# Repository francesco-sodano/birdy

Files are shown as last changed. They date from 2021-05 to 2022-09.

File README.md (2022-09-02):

<p align="center">
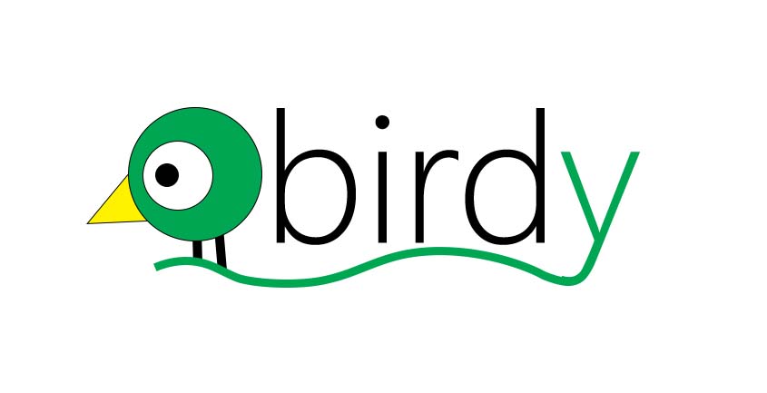
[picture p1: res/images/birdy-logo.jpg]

</p>

# Birdy - The Open-Source Smart Feeder to fight climate change
Birdy is a nicely designed wild bird feeder that takes photos, identifies and classifies birds. - based on Raspberry Pi, Azure IoT Edge and Azure Cognitive Service.

# Inspiration

Let's play a game! :)

***Question 1: Did you know that in many countries birdwatching is more popular than gardening?***

However, as you can't just sit around your bird feeder all the time, you miss out on a lot of action.

***Question 2: Did you know that birds play several essential and indispensable roles in the ecosystems they reside in and travel through?***

Birds raising broods end up acting as pest control agents by devouring insects and other organisms that harm the environment and crops. Migratory birds help in dispersal of seeds, leading to maintenance of biodiversity along their routes.

***Question 3: Did you know that bird feeders are helping migrating birds?***

Climate change does a lot more than just heat up our planet. Climate change can also cause more intense weather. That could mean more hurricanes, floods, heat waves, droughts, and even cold spells.
This extreme weather can be trouble for birds. Scientists have noticed that when extreme weather happens, fewer birds show up in the places they call home.
If birds are moving to other areas because of climate change, they may need our help and we may need to protect their new habitats.
Having bird feeders along their route will help to keep migrating birds energized to complete their journey forward. In months like the winter, bird feeders act almost like an oasis of food for these feathery creatures.

So what if will be able to combine all these in one single, open solution that:

1. Helps to identify, classify and register birds that are coming to visit our houses 
2. Shares those data worldwide, to identify new or established migration routes and define new natural reserves to fight the climate change
3. Works on our side to NOT miss out any visit you are having in your garden

these are the reasons why we created **Project Birdy**

<p align="center">
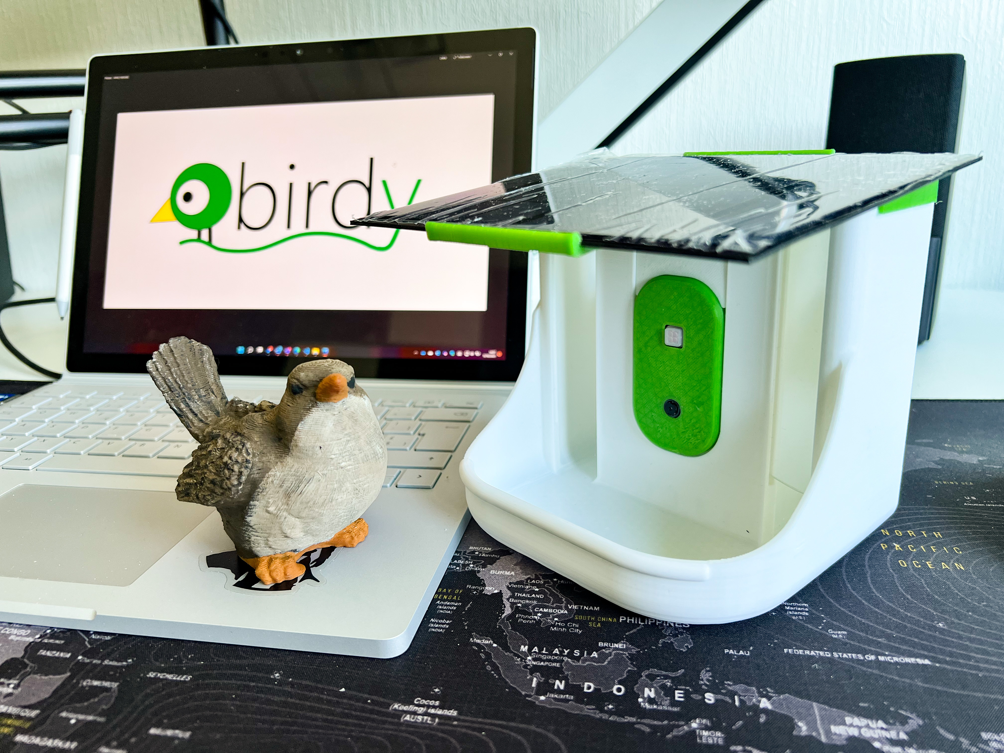
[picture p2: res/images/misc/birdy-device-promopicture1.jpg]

</p>

# The Project Repository

the repository is organized in this way:

1. *backend*: contains the contains the IaC for the backend deployment and the source code for the backend running on the infrastructure created.
2. *device*: contains the device STL for 3d printing and the software to run on the device.
3. *docs*: contains the step-by-step documentation for put in place the entire solution
4. *mobile*: contains the source code for the mobile app
5. *res*: contains static resources like images to be used in the doc files
6. *tools*: contains any additional resource you may need to put in place the solution

# The Device

The device is based on Raspberry Pi and use Azure IoT Edge framework.

<p align="center">
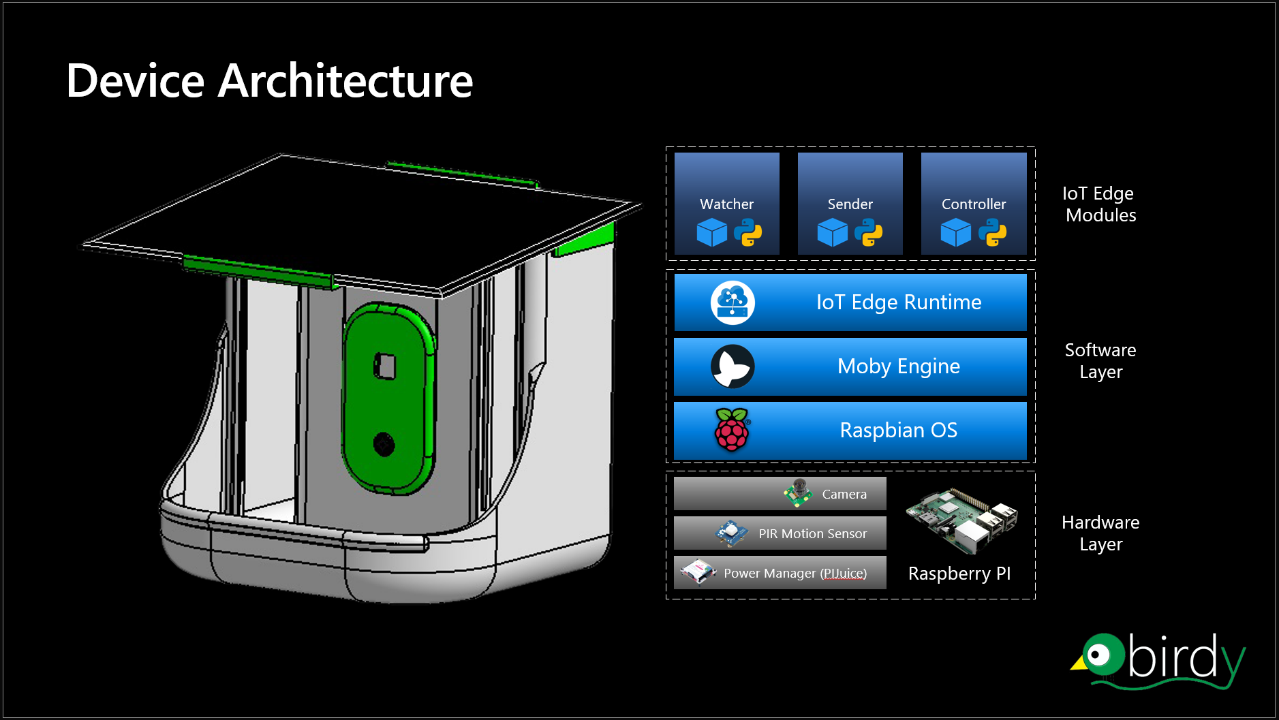
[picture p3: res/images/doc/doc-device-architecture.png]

</p>

More info can be found here: [The Device](https://github.com/francesco-sodano/birdy/blob/main/docs/device.md)

# The Back-end

# The Mobile App

# Notice

1. **Privacy** is always important for us. Birdy is designed and configured to have a very short focus range (5 cm max). it means that everything out of this range will be out-of-focus and blurred.
2. **Squirrels** are usually a common issues for bird feeders: There is actually no way to stop squirrels to come to the feeder but hey.. let's them eat too.. we are nature friends! :). Birdy as anyway a specific function to detect squirrel presence and don't collect pictures (also with an alert for the Birdy owner if configured).

# Table of Content

1. [Read Me](https://github.com/francesco-sodano/birdy/blob/main/README.md)
2. [The Device](https://github.com/francesco-sodano/birdy/blob/main/docs/device.md)
3. [Architecture](https://github.com/francesco-sodano/birdy/blob/main/docs/architecture.md)
4. [Deployment](https://github.com/francesco-sodano/birdy/blob/main/docs/deployment.md)
5. [Setup](https://github.com/francesco-sodano/birdy/blob/main/docs/instructions.md)

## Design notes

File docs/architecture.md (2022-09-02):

# Architecture

# Edge logical Architecture

The SmartBox is based on a Raspberry Pi architecture running Raspberry Pi OS Bullseye (Debian 11).

<p align="center">

</p>

On top of the OS, we have the IoT Edge Runtime (version 1.4): The IoT Edge service provides and maintains security standards on the IoT Edge device. The service starts on every boot and bootstraps the device by starting the rest of the IoT Edge runtime.

Azure IoT Edge relies on an OCI-compatible container runtime. Birdy is using Moby Engine for maximize support and compatibility: The Moby engine is the only container engine officially supported with IoT Edge.

The Birdy software are running as custom modules on the Azure Iot Edge service. there are three different custom modules running on the device:

- Watcher
- Sender
- Controller

## Watcher

## Sender

## Controller

# Back-End logical Architecture

## The Trained AI

## Data Layer

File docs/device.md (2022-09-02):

# The Device

The device is composed by hardware and software components.

There are different versions and variants of the device in this repository.

the macro-components of the device are the following:

1. Bird Feeder
2. Smart Box
3. Roof Top

## Bird Feeder

The Bird feeder is the main 3D Printed component of the device. it has the function of storing and deploy seeds and to handle the any version of the Smart Box.

<p align="center">
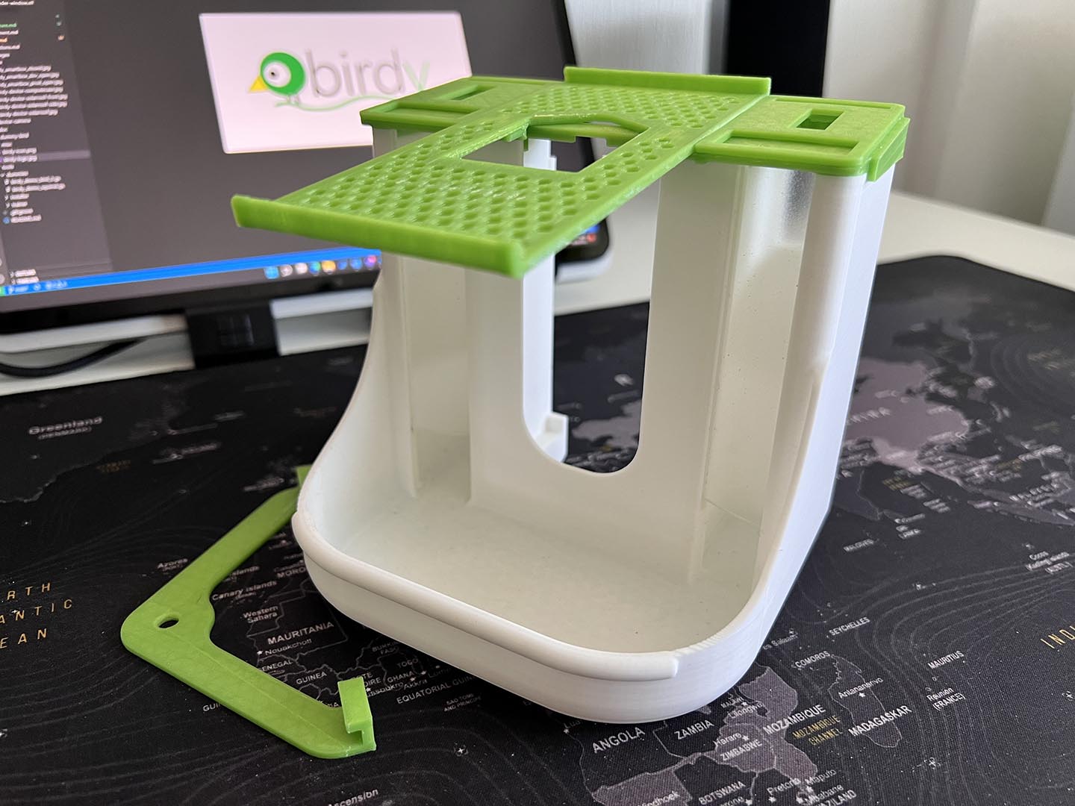
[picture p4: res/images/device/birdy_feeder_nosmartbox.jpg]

</p>

the Smart Box is detachable without compromise basic function of the feeder: it means you can use Birdy as standard feeder without the Smart Box.

## Smart Box

The Smart Box contians all the sensors, the battery and the compute for birdy.
It's easely detachable so you can bring it with you, leaving the feeder in its position.

<p align="center">
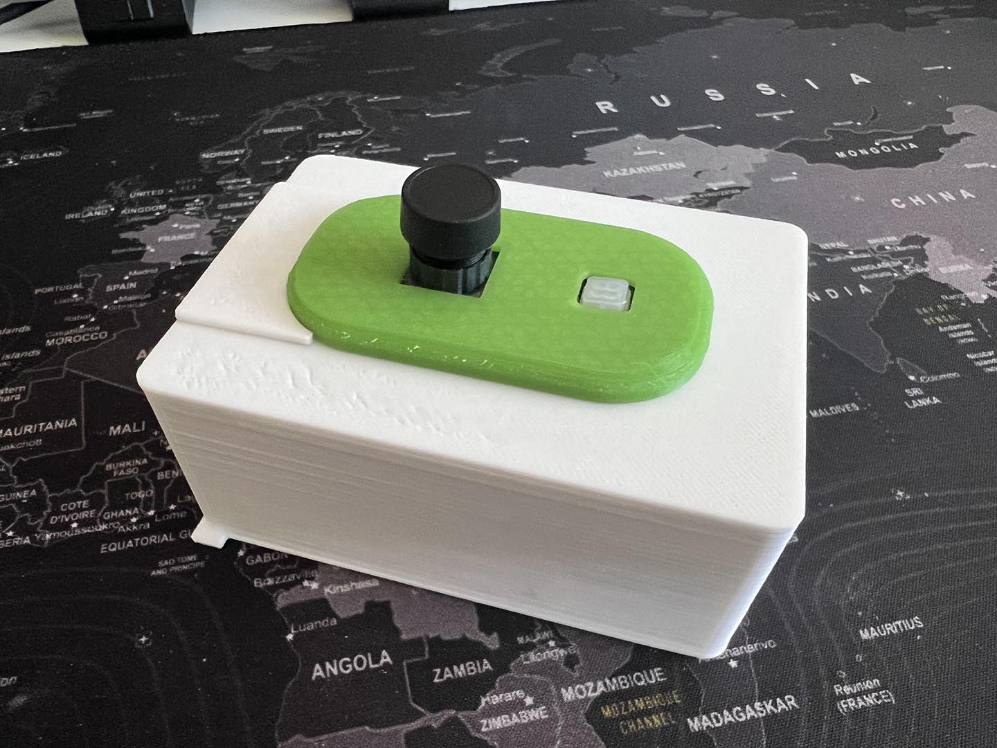
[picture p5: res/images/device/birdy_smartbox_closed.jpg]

</p>

The SmartBox is designed to work with a PiJuice Hat that works as power controller and can be configured and managed remotely: for example you can configure the smartbox to shutdown in the night and turn on again at dawn or shutdown when the battery power is at certain battery level and turn it on again when the solar panel rechanged the battery.

The Smart Box has two different versions:

1. **DEV Version**: this is based on Raspberry Pi 3 B+ and it's used for development. Raspberry Pi 3 B+ is able to handle direct connetion with Visual Studio Code for debugging. the battery life it's ok for few hours sessions.

<p align="center">
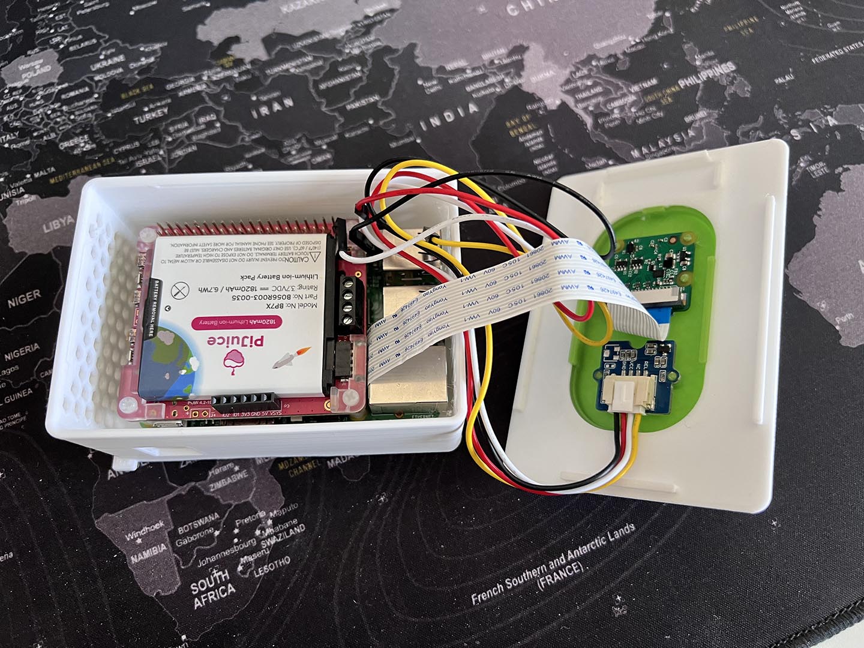
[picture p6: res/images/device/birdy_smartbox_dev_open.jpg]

</p>

2. **PROD Version**: this is based on Raspberry Pi Zero W and it's used for production. it's requires less power and has a better battery life to permit long sessions (up to one week).

<p align="center">
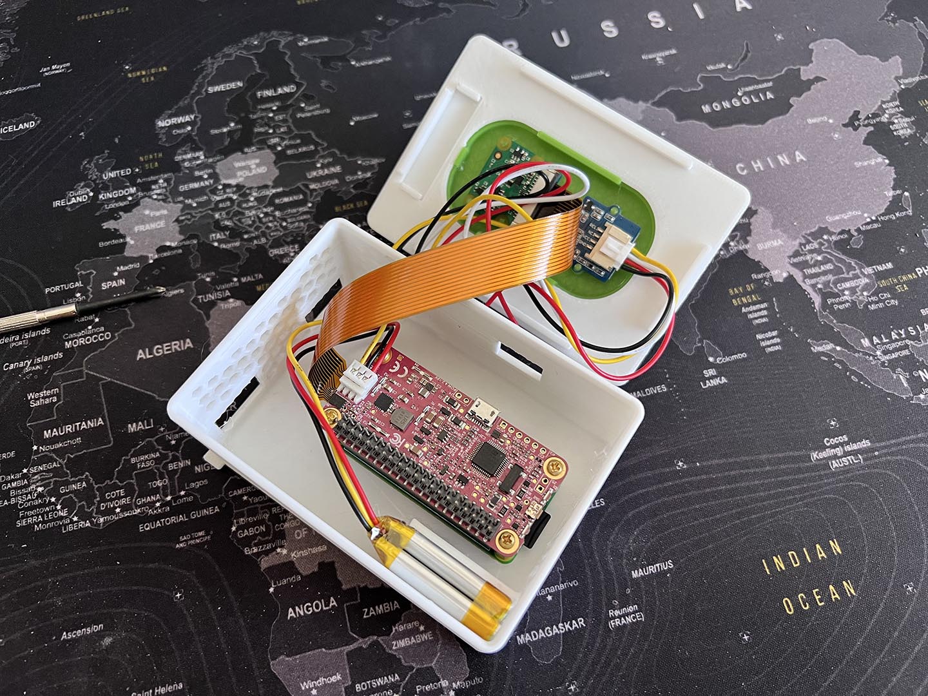
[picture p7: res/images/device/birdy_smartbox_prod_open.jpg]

</p>

The Smart box could be also directly connected to a power supply so Birdy can be always up and running.

## Roof Top

The Roof Top has also two different variants:

1. **Standard**: this is standard 3D printed roof.

2. **Solar Powered**: this is an enhanched version that includes a solar panel able to rechanrge the battery of the Smart Box and increase the autonomy of the device.

# Hardware Components

the **DEV Version** of the device requires the following hardware:

1. [Raspberry Pi 3 model B+](https://uk.pi-supply.com/products/raspberry-pi-3-model-b-plus?_pos=64&_sid=6161a3a4c&_ss=r1)
2. [Grove mini PIR motion sensor](https://www.seeedstudio.com/Grove-mini-PIR-motion-sensor-p-2930.html)
3. [Raspberry Pi camera board v2.1](https://uk.pi-supply.com/products/raspberry-pi-camera-board-v2-1-8mp-1080p?_pos=48&_sid=6161a3a4c&_ss=r)
4. [Raspberry Pi camera lens 160 degree](https://uk.pi-supply.com/products/camera-module-for-official-raspberry-pi-camera-board-v2-8mp-sensor-160-degree)
5. [PiJuice Standard with 1820mAh battery](https://uk.pi-supply.com/products/pijuice-standard)

the **PROD Version** of the device requires the following hardware:

1. [Raspberry Pi Zero W (with soldered header)](https://uk.pi-supply.com/products/raspberry-pi-zero-w-soldered-header)
2. [Grove mini PIR motion sensor](https://www.seeedstudio.com/Grove-mini-PIR-motion-sensor-p-2930.html)
3. [Raspberry Pi camera board v2.1](https://uk.pi-supply.com/products/raspberry-pi-camera-board-v2-1-8mp-1080p?_pos=48&_sid=6161a3a4c&_ss=r)
4. [Raspberry Pi camera lens 160 degree](https://uk.pi-supply.com/products/camera-module-for-official-raspberry-pi-camera-board-v2-8mp-sensor-160-degree)
5. [PiJuice Zero](https://uk.pi-supply.com/products/pijuice-zero?_pos=1&_sid=bd8682207&_ss=r)
6. [PiJuice Zero 1200mAh battery](https://uk.pi-supply.com/products/pijuice-zero-1200mah-battery?_pos=2&_sid=d94484a36&_ss=r)

The **Solar Version** of the device requires this additional hardware

1. [Solar Panel GH165x135 3.5W 6V USB](https://www.fruugoschweiz.com/35w-usb-solar-panel-digital-ladegerat-fur-mobile/p-88157157-183939064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)
# Component Matrix

The following table will help to navigate the different version and variant of the Birdy device

Feeder | Version | Variant | Component | Hardware
|:---:|:---:|:---:|:---:|:---:|
|Main|Dev|Standard| birdy-feeder-main.stl <br> birdy-feeder-roof.stl <br> birdy-feeder-hook.stl <br> birdy-feeder-window.stl (2) <br> birdy-smartbox-dev.stl <br> birdy-smartbox-top.stl <br> birdy-smartbox-filler.stl <br> birdy-smartbox-module.stl|[Raspberry Pi 3 model B+](https://uk.pi-supply.com/products/raspberry-pi-3-model-b-plus?_pos=64&_sid=6161a3a4c&_ss=r1) <br> [Grove mini PIR motion sensor](https://www.seeedstudio.com/Grove-mini-PIR-motion-sensor-p-2930.html) <br> [Raspberry Pi camera board v2.1](https://uk.pi-supply.com/products/raspberry-pi-camera-board-v2-1-8mp-1080p?_pos=48&_sid=6161a3a4c&_ss=r) <br> [Raspberry Pi camera lens 160 degree](https://uk.pi-supply.com/products/camera-module-for-official-raspberry-pi-camera-board-v2-8mp-sensor-160-degree)
|Main|Dev|Solar| birdy-feeder-main.stl <br> birdy-feeder-solarroof.stl <br> birdy-feeder-solarsupport.stl <br> birdy-feeder-hook.stl <br> birdy-feeder-window.stl (2) <br> birdy-smartbox-dev.stl <br> birdy-smartbox-top.stl <br> birdy-smartbox-filler.stl <br> birdy-smartbox-module.stl|[Raspberry Pi 3 model B+](https://uk.pi-supply.com/products/raspberry-pi-3-model-b-plus?_pos=64&_sid=6161a3a4c&_ss=r1) <br> [Grove mini PIR motion sensor](https://www.seeedstudio.com/Grove-mini-PIR-motion-sensor-p-2930.html) <br> [Raspberry Pi camera board v2.1](https://uk.pi-supply.com/products/raspberry-pi-camera-board-v2-1-8mp-1080p?_pos=48&_sid=6161a3a4c&_ss=r) <br> [Raspberry Pi camera lens 160 degree](https://uk.pi-supply.com/products/camera-module-for-official-raspberry-pi-camera-board-v2-8mp-sensor-160-degree) <br> [Solar Panel GH165x135 3.5W 6V USB](https://www.fruugoschweiz.com/35w-usb-solar-panel-digital-ladegerat-fur-mobile/p-88157157-183939064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)
|Main|Prod|Standard| birdy-feeder-main.stl <br> birdy-feeder-roof.stl <br> birdy-feeder-hook.stl <br> birdy-feeder-window.stl (2) <br> birdy-smartbox-dev.stl <br> birdy-smartbox-top.stl <br> birdy-smartbox-filler.stl <br> birdy-smartbox-module.stl|[Raspberry Pi Zero W (with soldered header)](https://uk.pi-supply.com/products/raspberry-pi-zero-w-soldered-header) <br> [Grove mini PIR motion sensor](https://www.seeedstudio.com/Grove-mini-PIR-motion-sensor-p-2930.html) <br> [Raspberry Pi camera board v2.1](https://uk.pi-supply.com/products/raspberry-pi-camera-board-v2-1-8mp-1080p?_pos=48&_sid=6161a3a4c&_ss=r) <br> [Raspberry Pi camera lens 160 degree](https://uk.pi-supply.com/products/camera-module-for-official-raspberry-pi-camera-board-v2-8mp-sensor-160-degree) <br> [PiJuice Zero](https://uk.pi-supply.com/products/pijuice-zero?_pos=1&_sid=bd8682207&_ss=r) <br> [PiJuice Zero 1200mAh battery](https://uk.pi-supply.com/products/pijuice-zero-1200mah-battery?_pos=2&_sid=d94484a36&_ss=r)
|Main|Prod|Solar| birdy-feeder-main.stl <br> birdy-feeder-solarroof.stl <br> birdy-feeder-solarsupport.stl <br> birdy-feeder-hook.stl <br> birdy-feeder-window.stl (2) <br> birdy-smartbox-dev.stl <br> birdy-smartbox-top.stl <br> birdy-smartbox-filler.stl <br> birdy-smartbox-module.stl|[Raspberry Pi Zero W (with soldered header)](https://uk.pi-supply.com/products/raspberry-pi-zero-w-soldered-header) <br> [Grove mini PIR motion sensor](https://www.seeedstudio.com/Grove-mini-PIR-motion-sensor-p-2930.html) <br> [Raspberry Pi camera board v2.1](https://uk.pi-supply.com/products/raspberry-pi-camera-board-v2-1-8mp-1080p?_pos=48&_sid=6161a3a4c&_ss=r) <br> [Raspberry Pi camera lens 160 degree](https://uk.pi-supply.com/products/camera-module-for-official-raspberry-pi-camera-board-v2-8mp-sensor-160-degree) <br> [PiJuice Zero](https://uk.pi-supply.com/products/pijuice-zero?_pos=1&_sid=bd8682207&_ss=r) <br> [PiJuice Zero 1200mAh battery](https://uk.pi-supply.com/products/pijuice-zero-1200mah-battery?_pos=2&_sid=d94484a36&_ss=r) <br> [Solar Panel GH165x135 3.5W 6V USB](https://www.fruugoschweiz.com/35w-usb-solar-panel-digital-ladegerat-fur-mobile/p-88157157-183939064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)

# Table of Content

1. [Read Me](https://github.com/francesco-sodano/birdy/blob/main/README.md)
2. [The Device](https://github.com/francesco-sodano/birdy/blob/main/docs/device.md)
3. [Architecture](https://github.com/francesco-sodano/birdy/blob/main/docs/architecture.md)
4. [Deployment](https://github.com/francesco-sodano/birdy/blob/main/docs/deployment.md)
5. [Setup](https://github.com/francesco-sodano/birdy/blob/main/docs/instructions.md)

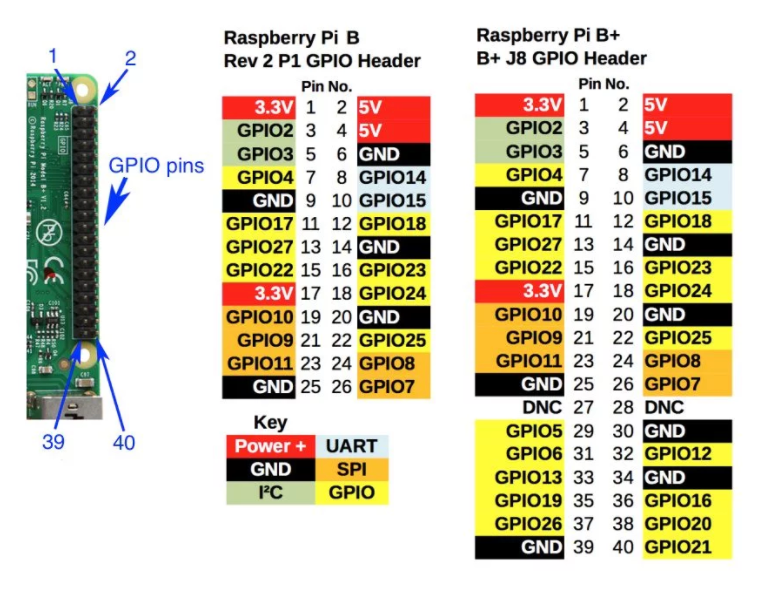
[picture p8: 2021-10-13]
res/images/doc/doc-pin-configuration.png

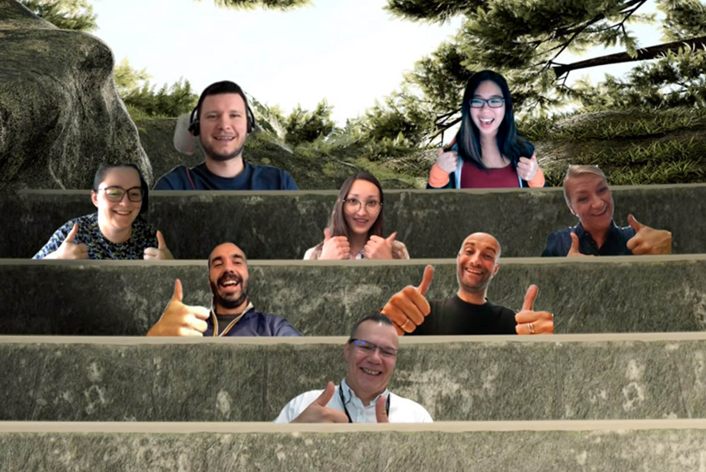
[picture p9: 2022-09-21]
res/images/misc/Birdy_Team.jpg

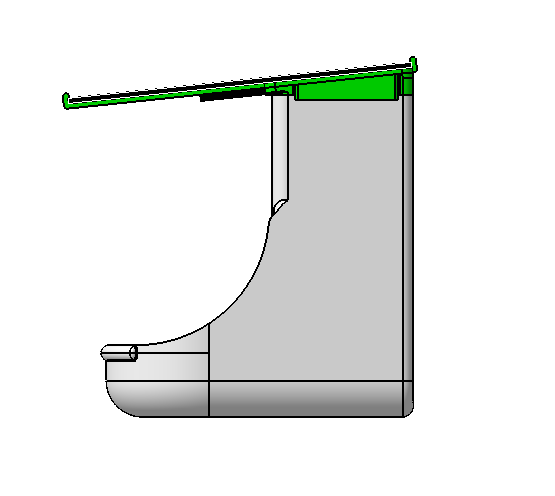
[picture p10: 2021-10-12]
res/images/device/birdy-device-solarroof-side.jpg

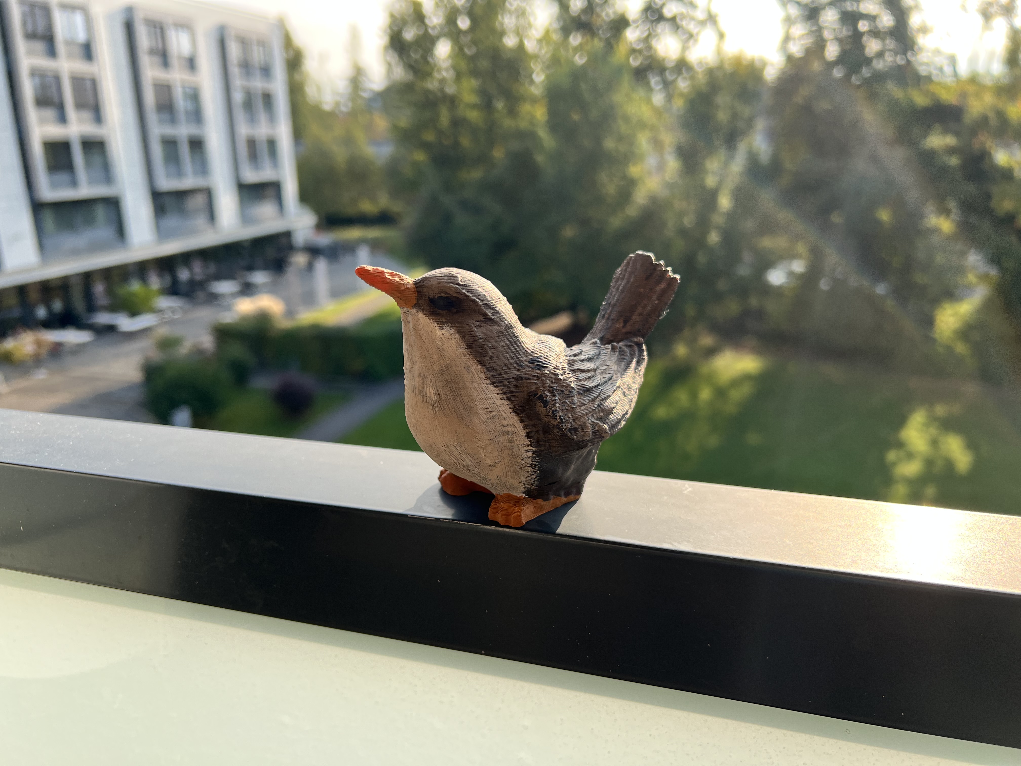
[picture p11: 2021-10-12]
res/images/dummy-bird/bird_1/dummy-bird_1_02.jpg

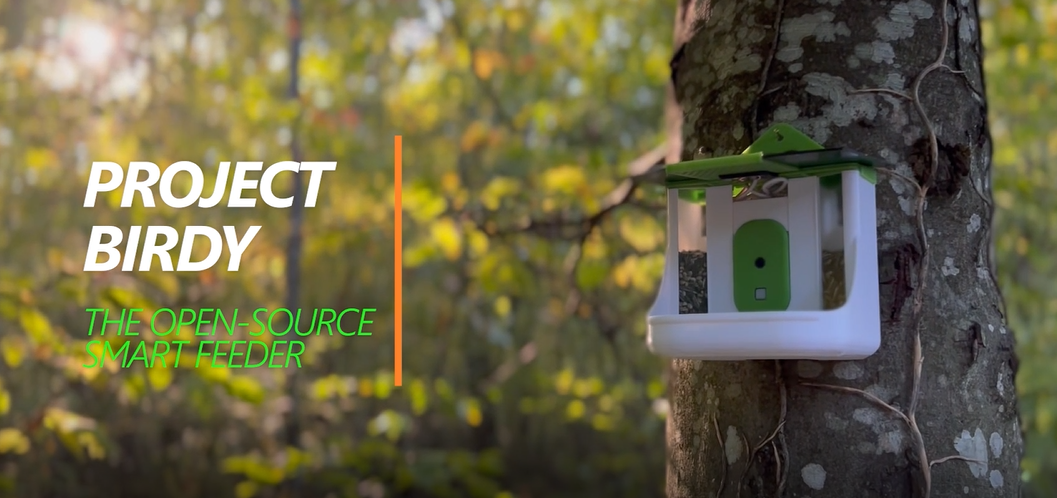
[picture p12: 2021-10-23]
res/images/misc/birdy-cover-image.png

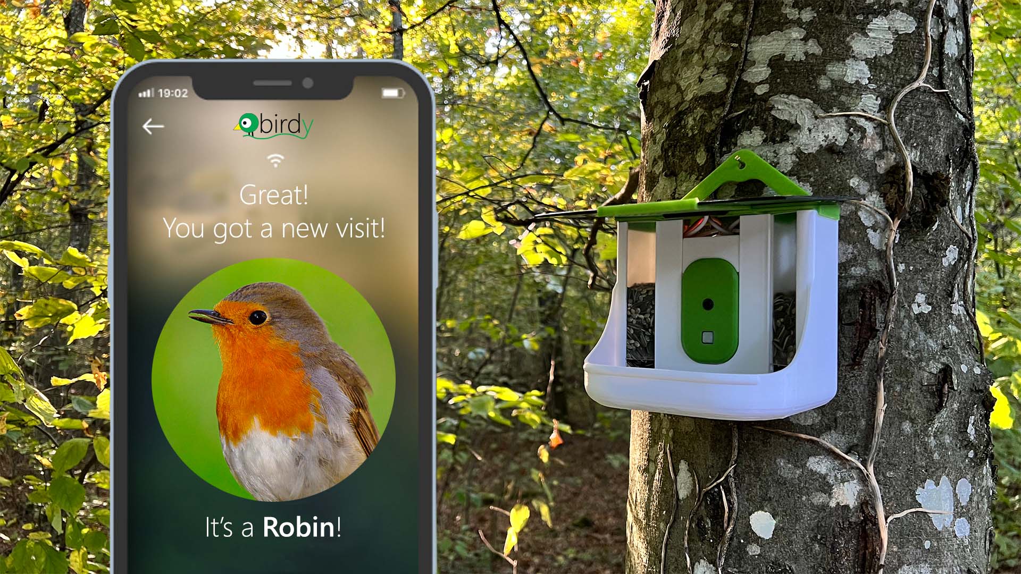
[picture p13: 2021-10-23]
res/images/misc/birdy-mobile-app.jpg

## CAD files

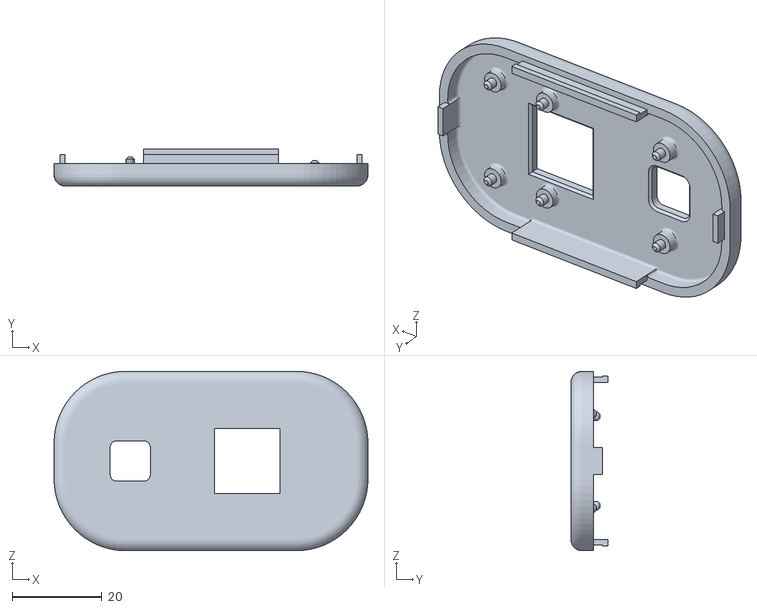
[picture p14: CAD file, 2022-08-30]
device/hardware/birdy-smartbox-module.stl
70.0 x 8.30 x 40.0

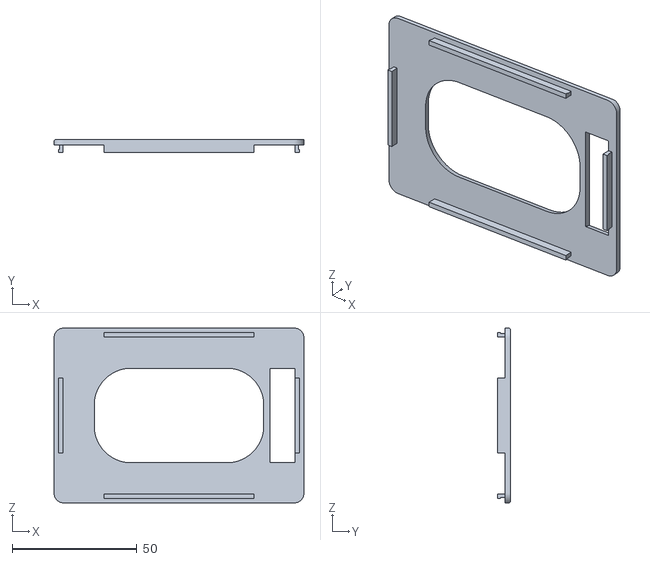
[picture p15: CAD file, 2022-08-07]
device/hardware/birdy-smartbox-top.stl
100.0 x 5.00 x 70.0

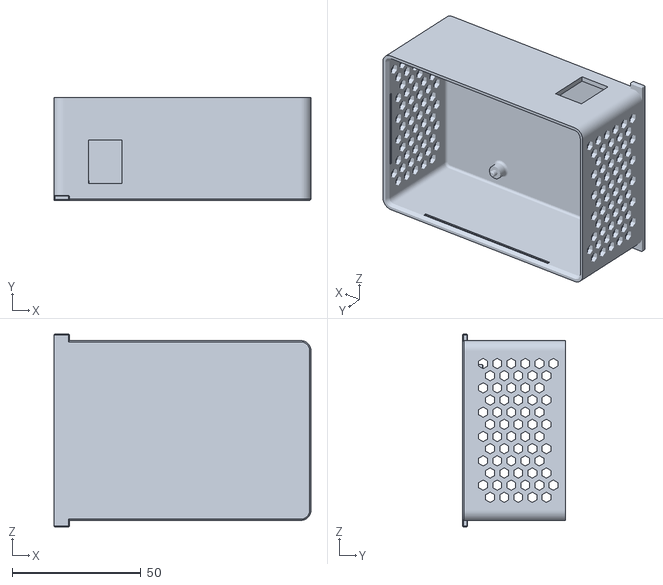
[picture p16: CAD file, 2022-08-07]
device/hardware/birdy-smartbox-dev.stl
100.0 x 40.0 x 75.0

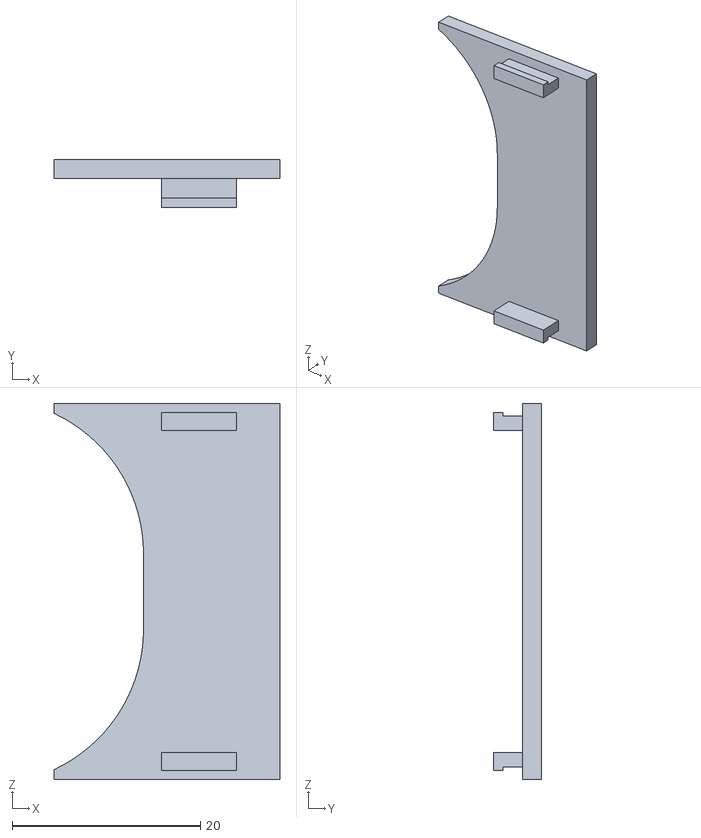
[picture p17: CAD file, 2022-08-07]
device/hardware/birdy-smartbox-filler.stl
24.0 x 5.10 x 40.0

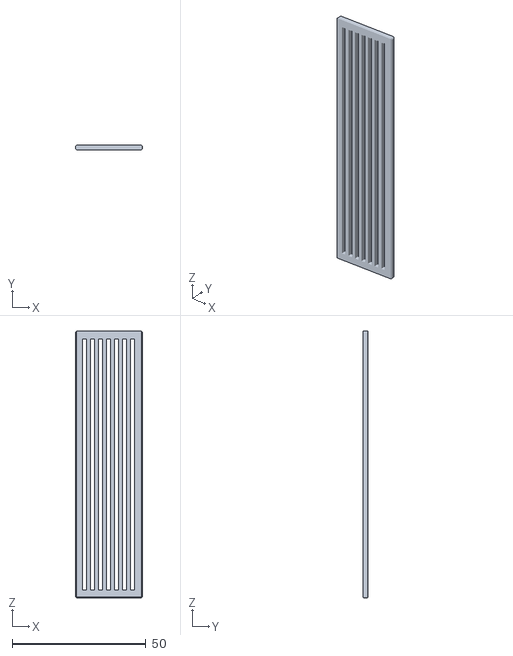
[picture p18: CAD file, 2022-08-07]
device/hardware/birdy-feeder-window.stl
25.0 x 2.00 x 100.0

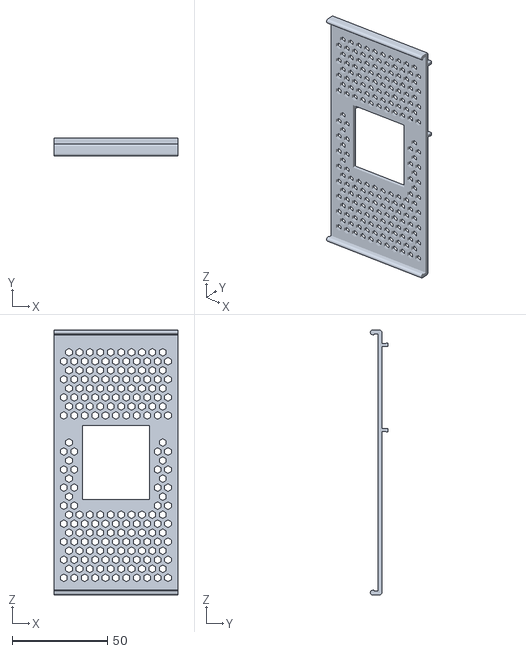
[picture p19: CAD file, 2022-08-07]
device/hardware/birdy-feeder-solarsupport.stl
65.0 x 9.20 x 139.0

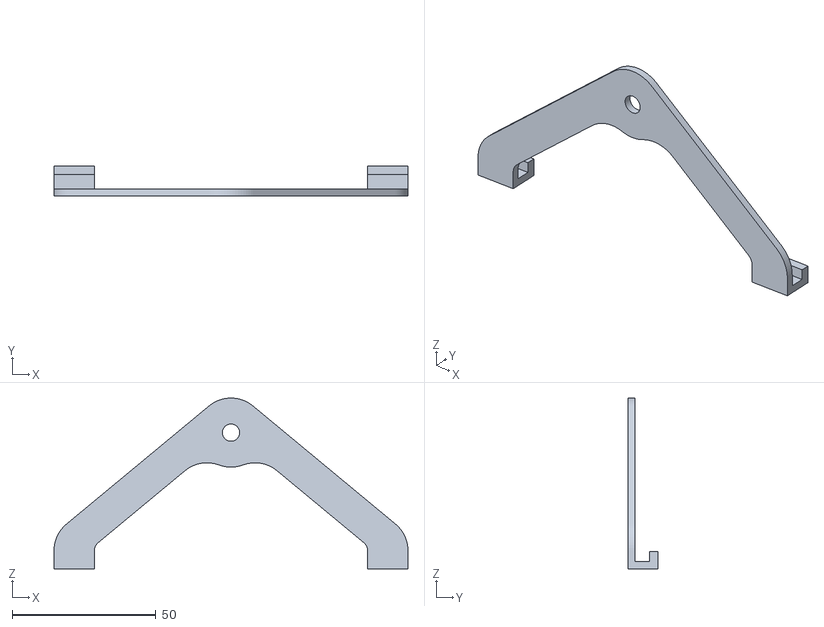
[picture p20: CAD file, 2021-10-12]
device/hardware/birdy-feeder-hook.stl
123.0 x 10.5 x 59.3

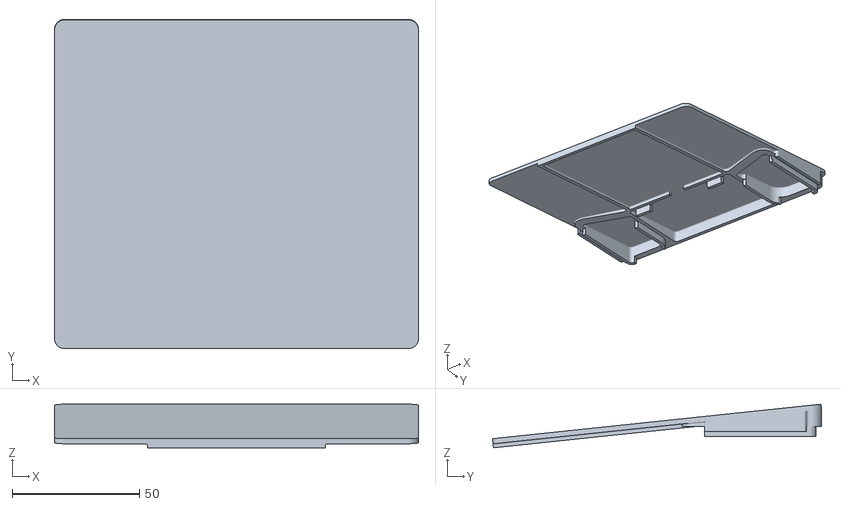
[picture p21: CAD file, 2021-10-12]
device/hardware/birdy-feeder-roof.stl
143.2 x 129.5 x 17.2

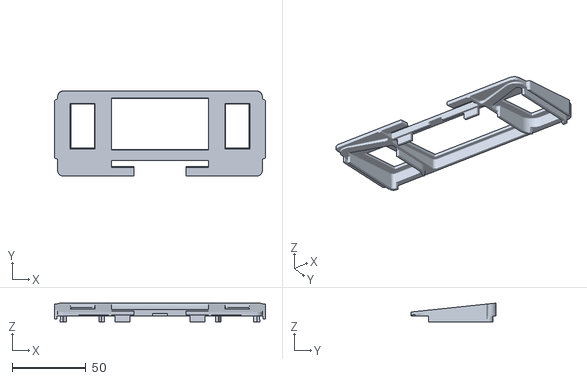
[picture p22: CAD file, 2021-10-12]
device/hardware/birdy-feeder-solarroof.stl
143.2 x 57.9 x 12.8

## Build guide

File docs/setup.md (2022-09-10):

# Setup Birdy

# Prepare Raspberry Pi

Raspberry Pi recommend the use of Raspberry Pi Imager to install an operating system on to your SD card. You will need another computer with an SD card reader to install the image.
The image required is 

## Enable ssh

In the boot volume, create a file without an extension and name it "ssh"

## Include Wi-Fi

In the boot volume, create a file called "wpa_supplicant.conf"

```python
ctrl_interface=DIR=/var/run/wpa_supplicant GROUP=netdev
update_config=1
country=CH
network={
    ssid="WIFI_SSID"
    scan_ssid=1
    psk="WIFI_PASSWORD"
    priority=1
    key_mgmt=WPA-PSK
}
```
## Setup 
Setup Raspberry: https://www.raspberrypi.org/documentation/configuration/wireless/headless.md

Secure Raspberry: https://www.raspberrypi.com/documentation/computers/configuration.html#securing-your-raspberry-pi

Passwordless access: https://www.raspberrypi.org/documentation/remote-access/ssh/passwordless.md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

## Install required Packages:

sudo apt update
sudo apt install git pijuice-base python3-pip python3-gpiozero
sudo apt install pip3 debugpy gpiozero picamera azure-eventhub azure-iot-device azure.storage.blob get-mac retrying

## Configure raspi-config

Configurations (with raspi-config):
 - Enable Camera
 - Enable I2C
 - Add Timezone

## Configure Camera settings

Modfiy the following line in the "Automatically load overlays for detected cameras"

```python
camera_auto_detect=0
```

Add this line to the "Enable DRM VC4 V3D driver" section

```python
dtoverlay=imx219,mediacontroller=0
```

Add the follwoing lines at the end of the "/boot/config.txt" file

```python
gpu_mem=32
start_file=start_x.elf
fixup_file=fixup_x.dat
```

## Setting the RTC (PiJuice)

After setting the date and time you must then copy the system time to the RTC with the command:

sudo hwclock -w

You can check this with:

sudo hwclock -r

When the Raspberry Pi shutsdown and then reboots you must copy the RTC time back to the system clock at boot and you can do this in /etc/rc.local (using sudo vi) with 

sudo hwclock -s.

# Device Optimization

## Disable Bluetooth

Edit /boot/config.txt and add the following line at the bottom:
    dtoverlay=disable-bt

then run:
    sudo systemctl disable hciuart.service
    sudo systemctl disable bluealsa.service
    sudo systemctl disable bluetooth.service

on the next boot you can run the following command to check that BT is disabled:

hcitool dev

## Disable HDMI

Add the line to /etc/rc.local to disable HDMI on boot. 
/usr/bin/tvservice -o

## Disable USB Chip

echo '1-1' |sudo tee /sys/bus/usb/drivers/usb/unbind

## Add Environment variable

Create a new file under /etc/profile.d to store the global environment variable(s). The name of the should be contextual so others may understand its purpose (for explample birdy.sh)

sudo touch /etc/profile.d/birdy.sh
sudo vi /etc/profile.d/birdy.sh

add the following line in vi.

export iotDeviceConnectionString="VALUE"
export birdDetectionVersion="20200330-1.0"

# Install Docker on the DEV device

curl -fsSL https://get.docker.com -o get-docker.sh
sudo sh get-docker.sh
sudo usermod -aG docker [user_name]
sudo reboot

# Install required software for Testing

curl https://packages.microsoft.com/config/debian/11/packages-microsoft-prod.deb > ./packages-microsoft-prod.deb;
sudo apt install ./packages-microsoft-prod.deb;
apt-get update -y;
apt-get install git -y;
git config --global user.email "email@github.com"
git config --global user.name "github"

# Visual Studio Extensions

Docker
markdownlint
Python
GitHub Pull Requests and Issues
IntelliCode
IntelliCode API Usage Examples

# disable logging for libcamera

append the folloing to /etc/environment file

LIBCAMERA_LOG_LEVELS=*:4

# Tensorflow required packages

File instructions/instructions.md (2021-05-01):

# Setup Birdy

# Raspberry Pi
Setup Raspberry: https://www.raspberrypi.org/documentation/configuration/wireless/headless.md
Secure Raspberry: https://www.raspberrypi.org/documentation/configuration/security.md
Passwordless access: https://www.raspberrypi.org/documentation/remote-access/ssh/passwordless.md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

Packages:

sudo apt update
sudo apt install git pijuice-base python3-pip python3-gpiozero
sudo apt install 
sudo apt install 
pip3 debugpy gpiozero picamera azure-eventhub azure-iot-device azure.storage.blob get-mac retrying

Configurations (with raspi-config):
 - Enable Camera
 - Enable I2C
 - Add Timezone

Setting the RTC (PiJuice)

After setting the date and time you must then copy the system time to the RTC with the command:

sudo hwclock -w

You can check this with:

sudo hwclock -r

When the Raspberry Pi shutsdown and then reboots you must copy the RTC time back to the system clock at boot and you can do this in /etc/rc.local (using sudo vi) with 

sudo hwclock -s.

Device Optimization

Disable Bluetooth
Edit /boot/config.txt and add the following line at the bottom:
    dtoverlay=pi3-disable-bt
then run:
    sudo systemctl disable bluetooth.service
on the next boot you can run the following command to check that BT is disabled:
hcitool dev

Disable HDMI
Add the line to /etc/rc.local to disable HDMI on boot. 
/usr/bin/tvservice -o
Reduce memory for video in /boot/config.txt
gpu_mem=16 

Disable USB Chip

echo '1-1' |sudo tee /sys/bus/usb/drivers/usb/unbind

Add Environment virable

Create a new file under /etc/profile.d to store the global environment variable(s). The name of the should be contextual so others may understand its purpose (for explample birddetector.sh)

sudo touch /etc/profile.d/birddetector.sh
sudo vi /etc/profile.d/birddetector.sh

add the following line in vi.

export iotDeviceConnectionString="VALUE"
export birdDetectionVersion="20200330-1.0"

# Trainer

pip install azure-cognitiveservices-vision-customvision

# Functions
pip install azure-storage-blob
pip install azure-cognitiveservices-vision-computervision

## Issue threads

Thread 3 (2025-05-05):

Update documentation

jshall77, 2025-05-05:
Hello,

I just wanted to send a note that the installation doesn't work any more.  The following packages are not available via apt or pip:

picamera azure-eventhub azure-iot-device azure.storage.blob

Can you please update the documentation?

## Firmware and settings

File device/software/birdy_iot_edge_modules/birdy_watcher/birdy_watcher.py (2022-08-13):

#!/usr/bin/env python3
# Project Birdy - v202110.1
# Copyright 2021 - Francesco Ares Sodano

import os
import json
from gpiozero import MotionSensor
from picamera import PiCamera
from datetime import datetime
from time import sleep

def main():
    # Importing settings
    try:
        configFile = './birdy_watcher.conf'
        with open(configFile, "rt") as file:
            deviceConfig = json.load(file)
            print ("File loaded")
    except:
        result = {"statusCode": 400, "statusDescription" : "Error loading configuration"}
        print ("Error loading configuration")
        return result
    # Configuring storage
    try:
        if (os.path.exists('/usr/src/app/birdy_files/')):
            print("Storage attached")
            deviceStorage= '/usr/src/app/birdy_files'
    except:
        result = {"statusCode": 400, "statusDescription" : "Storage not present"}
        print ("Storage not present")
        return result
    # Initializing sensors
    try:
        # Initializing Camera
        deviceCamera = PiCamera()
        deviceCamera.rotation = deviceConfig["device"]["camera"]["rotation"]
        deviceCamera.resolution = (deviceConfig["device"]["camera"]["resolution"]["w"], deviceConfig["device"]["camera"]["resolution"]["h"])
        deviceCamera.framerate = deviceConfig["device"]["camera"]["framerate"]
        deviceCamera.drc_strength = deviceConfig["device"]["camera"]["drc_strength"]
        deviceCamera.exposure_mode = deviceConfig["device"]["camera"]["exposure_mode"]
        # Initializing Motion PIR
        devicePIR = MotionSensor(deviceConfig["device"]["motionpir"]["pin"],queue_len=deviceConfig["device"]["motionpir"]["queue_len"],sample_rate=deviceConfig["device"]["motionpir"]["sample_rate"],threshold=deviceConfig["device"]["motionpir"]["threshold"])
        # Initializing Temperature and Humidity
        # TBD
        print("Sensors initialized")
    except:
        result = {"statusCode": 400, "statusDescription" : "Sensors Initialization error"}
        print ("Sensors Initialization error")
        return result
    # Motion detect Loop
    while True:
        devicePIR.wait_for_active()
        # wait for the right position of the bird
        sleep(2)
        birdImages = []
        while devicePIR.is_active:
            # take the time of the bird detection
            birdImageTime = datetime.utcnow()
            # take bird picture
            birdImageName = f"{deviceStorage}/images/birdimage{birdImageTime.strftime('%Y%m%d_%H%M%S')}.jpg"
            deviceCamera.capture(birdImageName)        
            birdImages.append(birdImageName)
            print("Image taken")
            sleep(2)
        # prepare the bird file
        birdFileTime = datetime.utcnow()
        birdFileName = f"{deviceStorage}/birdfile{birdFileTime.strftime('%Y%m%d_%H%M%S')}.json"
        birdFile = {
            "date" : birdImageTime.strftime("%d/%m/%Y"),
            "time" : birdImageTime.strftime("%H:%M:%S"),
            "temperature" : 20,
            "humidity" : 45,
            "images" : birdImages
        }
        # write bird file as JSON
        out_file = open(birdFileName,"w")
        json.dump(birdFile,out_file, indent = 4)
        out_file.close()
        # waiting time to reduce false positive
        sleep(5)
        #devicePIR.wait_for_inactive()
        # wait for the inactive queue to be empty
        #sleep(2)
        print("Bird captured")
if __name__ == "__main__": main()

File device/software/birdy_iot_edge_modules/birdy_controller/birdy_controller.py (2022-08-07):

#!/usr/bin/env python3
# Project Birdy - v202110.1
# Copyright 2021 - Francesco Ares Sodano

import os
import json
from pijuice import PiJuice
from gpiozero import CPUTemperature
from datetime import datetime
from time import sleep
from azure.iot.device.aio import IoTHubDeviceClient, IoTHubModuleClient
from azure.iot.device import Message
from azure.storage.blob import BlobServiceClient, BlobClient, ContainerClient
from azure.core.exceptions import AzureError, ResourceExistsError

def main():
    # Importing settings
    try:
        configFile = f'{os.path.dirname(os.getcwd())}/birdy_config.json'
        with open(configFile, "rt") as file:
            deviceConfig = json.load(file)
            print ("File loaded")
    except:
        result = {"statusCode": 400, "statusDescription" : "Error loading configuration"}
        print ("Error loading configuration")
        return result

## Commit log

2021-04-28 first partial ARM Template / first Birdy class
2021-04-28 arm template - parameters added
2021-04-28 ARM Template - added some resources
2021-04-29 ARM Template Updated / trainer first version
2021-04-29 test file created ARM Error
2021-04-29 Fix ARM Template error
2021-04-29 Fix dependancy ARM Template
2021-05-15 full infrastructure ARM Template
2021-05-15 Fixed ARM Tempalted Error for consumer vision keys
2021-10-12 updated STL files for 3D Printing
    [birdy-compute-case-dev.stl, birdy-compute-casefiller.stl, birdy-compute-casetop.stl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]
2021-10-12 Updated Device images
2021-10-12 Uploaded first pictures of from the device camera
2021-10-14 Update device documentation
2021-10-16 Updatd camera position to be more central
    [birdy-compute-modulecover.stl]
2022-08-06 Updated Device Documentation
2022-08-07 Repo Reorg and Doumcnetation Update
    [birdy-compute-case-dev.stl, birdy-compute-casefiller.stl, birdy-compute-casetop.stl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]
2022-08-25 Camera settgins json
2022-08-30 Updated Module schema STL
    [birdy-smartbox-module.stl]
2022-09-02 device tester tools
2022-09-05 Updated Sensor Testers scripts
2022-09-10 Updated Model and Labels
    [birdy_labels.csv]
2022-09-10 Add test image for model
    [birdy_labels.csv]
2022-09-10 Added addtional tflite model
    [birdy_labels.csv]
2022-09-12 Update classifier and test images
    [birdy_labels.csv]
2022-09-12 Updated Camera test with overlay
2022-09-12 Updated Sensor Tester with overlay
2022-09-18 New sensor tester video
2024-08-02 Bump keras in /device/software/birdy_iot_edge_modules/birdy_watcher
    Bumps [keras](https://github.com/keras-team/keras) from 2.10.0 to 2.13.1.
    - [Release notes](https://github.com/keras-team/keras/releases)
    - [Commits](https://github.com/keras-team/keras/compare/v2.10.0...v2.13.1)
    ---
    updated-dependencies:
    - dependency-name: keras
    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
